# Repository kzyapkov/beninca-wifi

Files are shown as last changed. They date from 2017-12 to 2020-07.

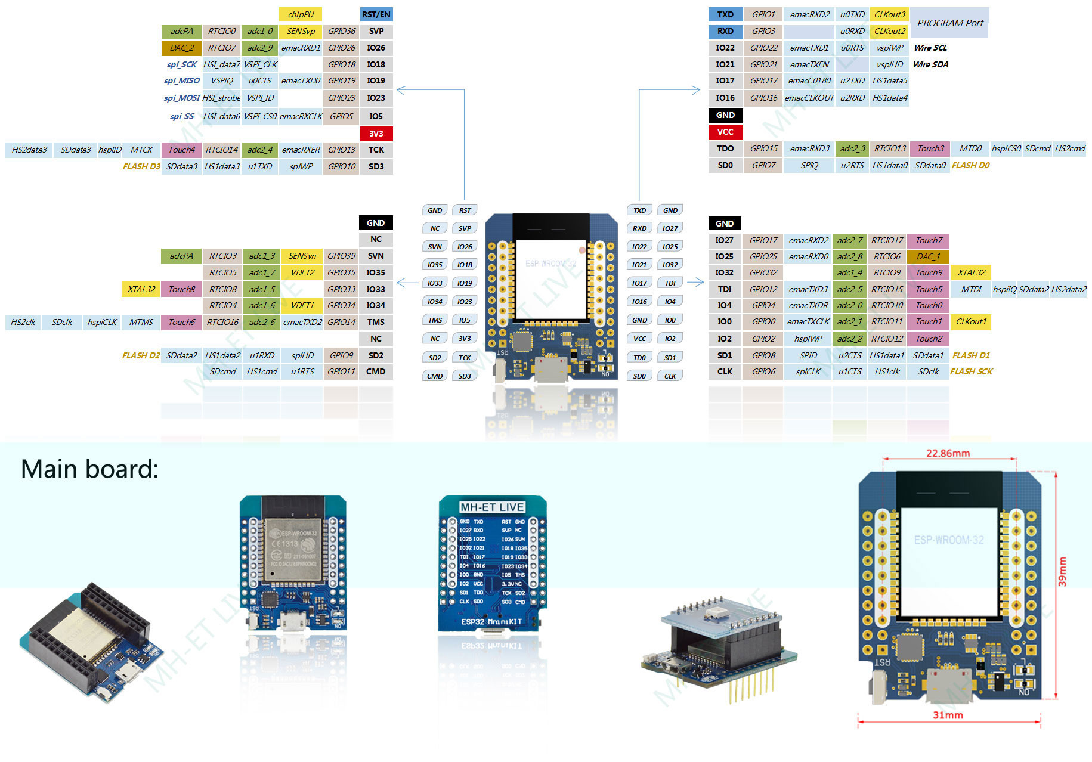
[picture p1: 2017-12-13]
doc/minikit.jpg

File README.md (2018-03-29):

# Beninca Core WiFi addon

## Overview

This device adds WiFi connectivity and remote control to a
[Beninca](http://beninca.com/)
[CORE](https://www.beninca.com/en/accessories/control-panels/swinging-gates.html)
control panel installed in a number of sliding and swinging gate controllers.

## Hardware

The brain is an ESP32 in an
[ESP32 MiniKIT](http://forum.mhetlive.com/topic/8/new-mh-et-live-minikit-for-esp32).

Power comes from the CORE board itself, supply is rated at 24VAC, up to 200mA.
This gets rectified and stepped down twice:

 * Amtec AMSRW-78Z, quite pricy but tiny and to specs, steps down to 12V which
   are used for the relays
 * A cheap ebay-sourced DSN-MINI-360 board steps it down further to 3.3V which
   feed the ESP32.

This power scheme is flawed -- the on-board LDO responsible for powering the
devkit through USB gets fried if you feed it 3.3V. Don't replicate that.
Feed the devkit with 5V instead, or use a bare ESP32 module.

The module has outputs for `STOP` and `P.P` on the controller via relays and
senses the `SCA` from CORE to know the position of the gate.

## Interface

JSON messages are exchanged over MQTT and allow for control and monitoring.
`beninca.py` contains a custom home-assistant component which provides a
`cover` device. Place it in `<config dir>/custom_components/cover/` and add
some configuration:

```
cover:
  - platform: beninca
    name: front_gate
    device_id: beninca-??????
    device_class: garage
```

## License

Copyright 2017 Kiril Zyapkov

This code is released under GPLv2, see `LICENSE` for details

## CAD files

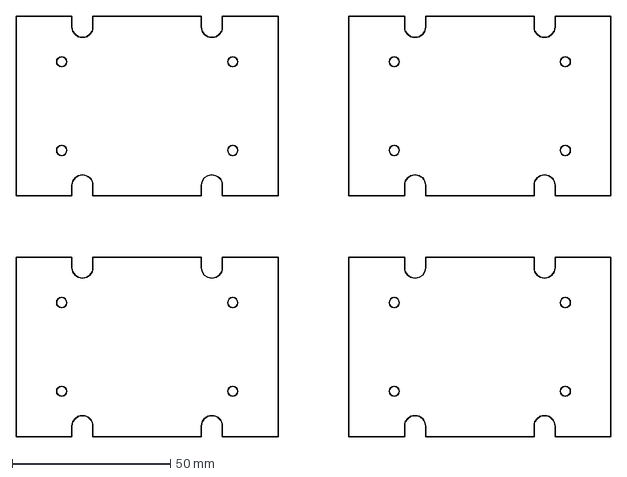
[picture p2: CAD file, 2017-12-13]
doc/board_layout.dxf
187.7 x 132.6 mm

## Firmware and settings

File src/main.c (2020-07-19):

#include "mgos.h"
#include "mgos_mqtt.h"
#include "mgos_ota.h"
#include "beninca.h"


static struct beninca_status last_status;
static bool uplink_ok = false;
static double uplink_since = 0;

const char * _topic(const char *t) {
    static char topic[256];
    snprintf(topic, sizeof(topic), "%s/%s", mgos_sys_config_get_device_id(), t);
    return topic;
}

static uint32_t btn_count = 0;
void _on_button(int pin, void *arg) {
    LOG(LL_INFO, ("button event on pin %d: %d",
                  pin, mgos_gpio_read(pin)));
    btn_count++;
    (void) pin;
    (void) arg;
}

void publish_lock() {
    char *s = last_status.control.stop_hold ? "ON" : "OFF";
    mgos_mqtt_pub(_topic("beninca/lock"), s, strlen(s),
                  1 /*qos*/, true /*retain*/);
}

void publish_status() {

    // TODO: remember when publishing fails and re-pubhish on reconnect
    // TODO: observe connected status and num unsent bytes

    struct beninca_status *status = &last_status;
    struct mbuf buf;
    mbuf_init(&buf, 50);
    struct json_out msg = JSON_OUT_MBUF(&buf);
    json_printf(&msg,
            "{moving:%B,since:%.2f,dir:%Q,time:%.2f,"
            "ctl:{stop_hold:%B,stop:%B,pp:%B},"
            "sca:{is:%B,since:%.2f,was:%B,lasted:%.2f},btn:%u}",
            status->moving, status->since, beninca_dir_str(status->dir), status->time,
            status->control.stop_hold, status->control.stop_strobe, status->control.pp_strobe,
            status->sca.is, status->sca.since, status->sca.was, status->sca.lasted,
            btn_count);
    LOG(LL_INFO, ("status: %.*s", buf.len, buf.buf));
    if (!mgos_mqtt_pub(_topic("beninca/status"), buf.buf, buf.len, 1 /*qos*/, true /*retain*/)) {
        LOG(LL_INFO, ("error publishing!"));
    }
    mbuf_free(&buf);

    publish_lock();
}

void _on_command(struct mg_connection *nc, const char *_topic_str,
              int _topic_len, const char *msg, int msg_len,
              void *ud) {

    bool ret = false;
    char *cmd = NULL;
    int req_id = -1;
    json_scanf(msg, msg_len, "{cmd:%Q,req_id:%d}", &cmd, &req_id);
    if (cmd == NULL) {
        LOG(LL_INFO, ("no cmd in %.*s", msg_len, msg));
        return;
    }

    if (strcmp(cmd, "stop_push") == 0) {
        beninca_stop();
        ret = true;
    } else if (strcmp(cmd, "stop_hold") == 0) {
        beninca_stop_hold();
        ret = true;
    } else if (strcmp(cmd, "stop_release") == 0) {
        beninca_stop_release();
        ret = true;
    } else if (strcmp(cmd, "pp_push") == 0) {
        beninca_pp();
        ret = true;
    } else if (strcmp(cmd, "get_status") == 0) {
        publish_status();
        ret = true;
    } else {
        LOG(LL_WARN, ("unknown command: %s", cmd));
    }

    struct mbuf buf;
    mbuf_init(&buf, 50);
    struct json_out out = JSON_OUT_MBUF(&buf);
    json_printf(&out, "{req_id:%d,cmd:%Q,resp:%B}", req_id, cmd, ret);
    mgos_mqtt_pub(_topic("beninca/response"), buf.buf, buf.len,
                  1 /*qos*/, false /*retain*/);

    free((void *)cmd);
    mbuf_free(&buf);

    (void) nc;
    (void) _topic_str;
    (void) _topic_len;
}

void _on_lock(struct mg_connection *nc, const char *_topic,
              int _topic_len, const char *msg, int msg_len,
              void *ud) {
    bool was_locked = last_status.control.stop_hold;
    int is_locked = -1;
    if (msg_len >= 2 && strncasecmp(msg, "on", 2) == 0) {
        is_locked = 1;
        beninca_stop_hold();
    } else if (msg_len >= 3 && strncasecmp(msg, "off", 3) == 0) {
        is_locked = 0;
        beninca_stop_release();
    }

    if (is_locked < 0 || is_locked == was_locked) publish_lock();

    (void) nc;
    (void) _topic;
    (void) _topic_len;
}
void _beninca_status_cb(const struct beninca_status *status) {
    last_status = *status;
    publish_status();
}

void _mqtt_net_ev(struct mg_connection *nc, int ev,
                    void *ev_data MG_UD_ARG(void *user_data)) {

    switch (ev) {
        case MG_EV_MQTT_CONNACK:
            uplink_ok = true;
            uplink_since = mg_time();
            // push update
            break;
        case MG_EV_CLOSE:
            uplink_ok = false;
            uplink_since = mg_time();
            break;
        default:
            break;
    }

    (void) nc;
    (void) user_data;
}


enum mgos_app_init_result mgos_app_init(void) {
    memset(&last_status, 0, sizeof(last_status));
    // LED and user button
    mgos_gpio_set_mode(mgos_sys_config_get_pinmux_led(), MGOS_GPIO_MODE_OUTPUT);
    mgos_gpio_set_button_handler(mgos_sys_config_get_pinmux_button(),
        MGOS_GPIO_PULL_NONE, MGOS_GPIO_INT_EDGE_NEG, 200 /*debounce_ms*/,
        _on_button, NULL);

    beninca_init(_beninca_status_cb);

    // MQTT
    mgos_mqtt_add_global_handler(_mqtt_net_ev, NULL);
    mgos_mqtt_sub(_topic("beninca/command"), _on_command, NULL);
    mgos_mqtt_sub(_topic("beninca/lock/command"), _on_lock, NULL);

    // Stop timer on update
    // mgos_event_add_handler(MGOS_EVENT_OTA_BEGIN, update_cb, NULL);
    // mgos_upd_set_event_cb(update_cb, NULL);

    return MGOS_APP_INIT_SUCCESS;
}

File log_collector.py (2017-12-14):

#!/usr/bin/env python2

import sys
import os
import os.path as p
import logging
import argparse
from datetime import datetime
from logging.handlers import TimedRotatingFileHandler, SocketHandler

import serial

_logdir = p.realpath('logs')

parser = argparse.ArgumentParser(
    formatter_class=argparse.ArgumentDefaultsHelpFormatter)
parser.add_argument('--port', default=os.environ.get('MOS_PORT', '/dev/ttyUSB0'),
                    help="Which serial port to use")
parser.add_argument('--baud', default=115200,
                    help="BAUD rate for the serial port")
parser.add_argument('--log-dir', nargs="?", default=_logdir,
                    help="Where to store log files")
parser.add_argument('--log-addr', nargs="?",
                    help="Where to netcat log data, host:port")
parser.add_argument('-q', '--quiet', default=False,
                    help="Disable HAC log on stdout")


def applog(quiet=False):
    log = logging.getLogger('hacvisor')
    log.setLevel(logging.DEBUG)
    hndlr = logging.StreamHandler(sys.stdout)
    hndlr.setLevel(logging.INFO if quiet else logging.DEBUG)
    hndlr.setFormatter(logging.Formatter(
        u"%(asctime)s %(levelname)-5.5s %(message)s"))
    log.addHandler(hndlr)
    return log


def shelog(log_dir=None, log_addr=(None, None)):
    log = logging.getLogger('she')
    log.setLevel(logging.DEBUG)
    fmtr = logging.Formatter(u"%(asctime)s %(message)s")

    if log_dir:
        hndlr = TimedRotatingFileHandler(p.join(log_dir, 'serial.log'),
            when="midnight", interval=1, backupCount=14, encoding="utf8")
        hndlr.setLevel(logging.DEBUG)
        hndlr.setFormatter(fmtr)
        log.addHandler(hndlr)

    if log_addr[0]:
        hndlr = SocketHandler(*log_addr)
        hndlr.setLevel(logging.DEBUG)
        hndlr.setFormatter(fmtr)
        log.addHandler(hndlr)

    return log

class Backtracer(object):

    START_DELIM = '--- BEGIN CORE DUMP ---'
    END_DELIM =   '---- END CORE DUMP ----'
    LOGBUF_LINES = 300

    def __init__(self, dir_, prefix):
        self.dir = p.realpath(dir_)
        self.prefix = prefix
        self.logbuf = []
        self.backtrace = None
        self.created = None

    def add(self, line):
        if not self.backtrace:
            if line.find(self.START_DELIM) != -1:
                self.backtrace = [line]
                self.created = datetime.now()
                return

            self.logbuf.append(line)
            while len(self.logbuf) > self.LOGBUF_LINES:
                self.logbuf.pop(0)

        else:
            self.backtrace.append(line)
            if line.find(self.END_DELIM) != -1:
                self.emit()
                self.backtrace = None
                self.created = None
                self.logbuf = []

    def emit(self):
        fn = "{}_{}.coredump".format(
                self.prefix, self.created.strftime("%Y%m%d-%H%M"))

        with open(p.join(self.dir, fn), 'w') as fp:
            for line in self.logbuf + self.backtrace:
                fp.write(line)
                if not line.endswith('\n'): fp.write('\n')

def main():
    args = parser.parse_args()
    print("Starting with: %s" % (args,))

    log = applog(args.quiet)

    if args.log_dir:
        if not os.path.exists(args.log_dir):
            try:
                os.mkdir(args.log_dir)
            except (OSError, IOError):
                log.error("%s did not exist and we could not create it")

        if not os.path.isdir(args.log_dir) or not os.access(args.log_dir, os.W_OK):
            log.error("%s: not a directory or not writable", args.log_dir)
            sys.exit(1)
        log.info("Log files will be stored in %s", args.log_dir)

    (host, port) = (None, None)
    if args.log_addr:
        try:
            host, port = args.log_addr.split(':')
            port = int(port)
            log.info("Log records will be sent via TCP to %s:%d", host, port)
        except (TypeError, ValueError) as e:
            log.error("Invalid --log-addr='%s': %s", args.log_addr, e)
            sys.exit(3)

    she = shelog(args.log_dir, (host, port))
    bt = Backtracer(args.log_dir, '')
    try:
        port = serial.Serial(args.port, baudrate=args.baud, timeout=0.2)
    except Exception as e:
        log.error("Unable to open serial port %s: %s", args.port, e)
        sys.exit(2)

    try:
        while True:
            line = port.readline()
            if not len(line):
                continue

            bt.add(line)

            log.info("%s", line.rstrip("\r\n"))
            if line.endswith('\n'):
                she.info("| %s", line.rstrip("\r\n"))
            else:
                she.info("  %s", line.rstrip("\r\n"))

            [h.flush() for h in she.handlers]

    except KeyboardInterrupt:
        port.close()
        sys.exit(0)
    except Exception as e:
        log.exception("Unhandled mainloop error: %s", e)
        port.close()
        sys.exit(15)


if __name__ == '__main__':
    main()

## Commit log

2017-12-13 make hw timer ISR safer
2017-12-14 bump mongoose with yet another wifi fix, add log_collector.py
    [log_collector.py]
